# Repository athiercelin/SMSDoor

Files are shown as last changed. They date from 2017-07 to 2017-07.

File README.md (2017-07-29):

# SMS Door Control
This project allows you to build a SMS controlled door buzzer with minimal impact to existing infrastructure.

**This is an active project that will change as often as required**

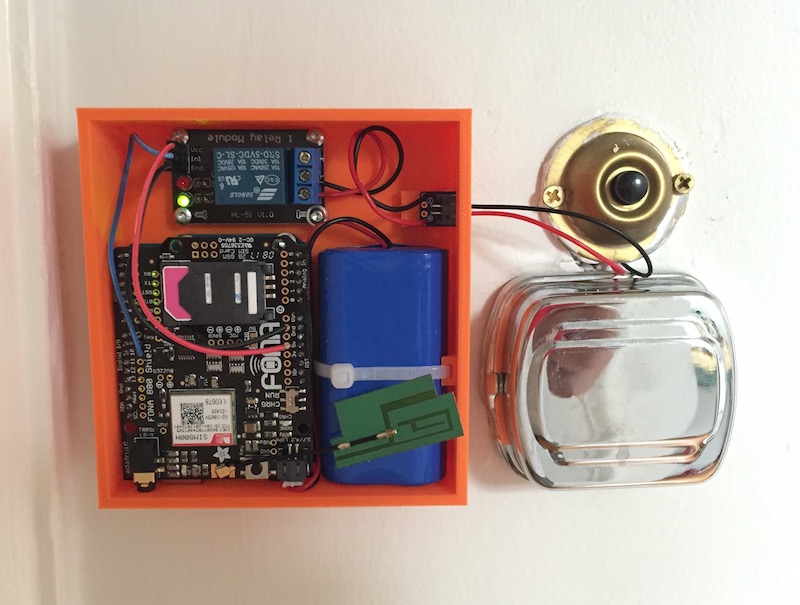
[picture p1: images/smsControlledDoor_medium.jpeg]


## Premises
I rent an old apartment in SF. There is no door man so deliveries are difficult.

To circumvent this, I created this project which allow the delivery company to gain temporary access to the lobby using a text message.

At the same time, I get notified and have remote control to the system through the text interface.

Finally, because I rent, I wanted a none intrusive and damaging system.

## Bill of Materials

|Picture|Label|Comments|
|---|----|----|
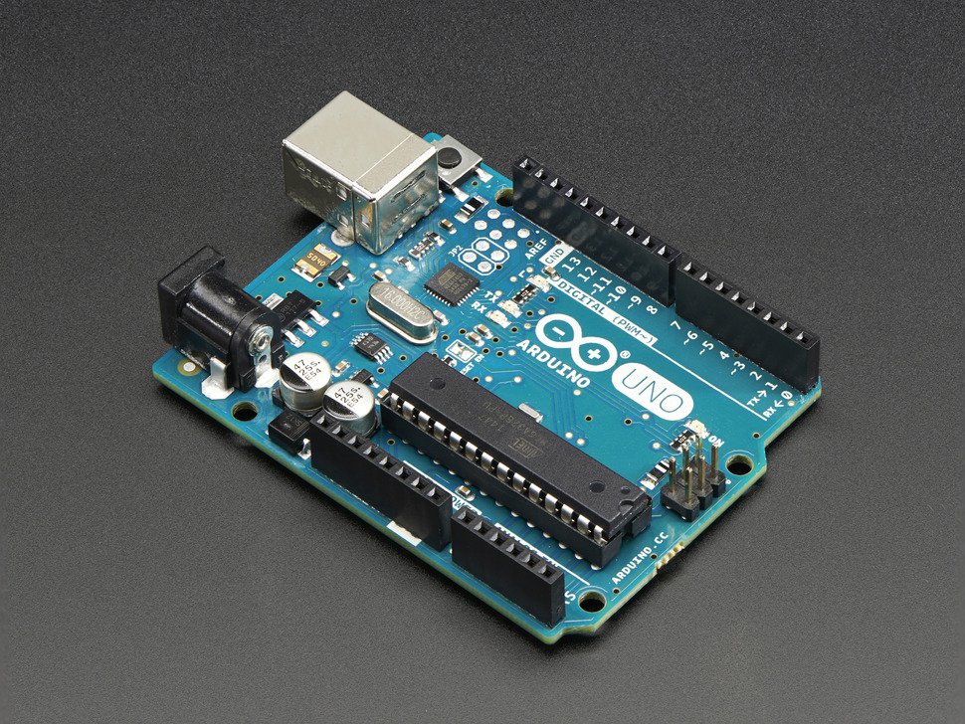
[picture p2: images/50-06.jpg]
|  | [Arduino Uno R3 (Atmega328 - assembled)](https://www.adafruit.com/product/50) | The brain of the project|
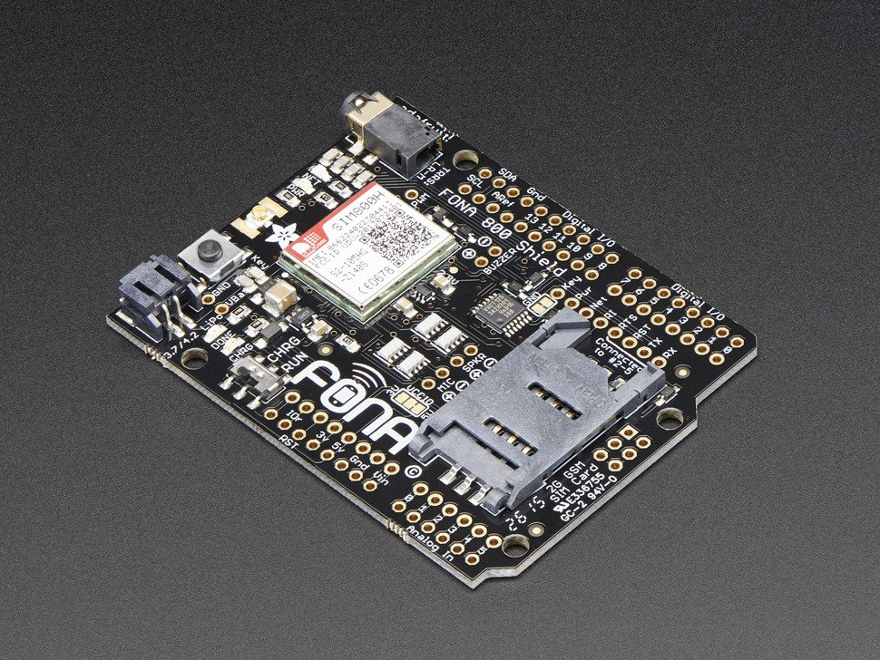
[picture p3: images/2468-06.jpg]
|  | [Adafruit FONA 800 Shield - Voice/Data Cellular GSM for Arduino](https://www.adafruit.com/product/2468) | Making your life easy to access by SMS|
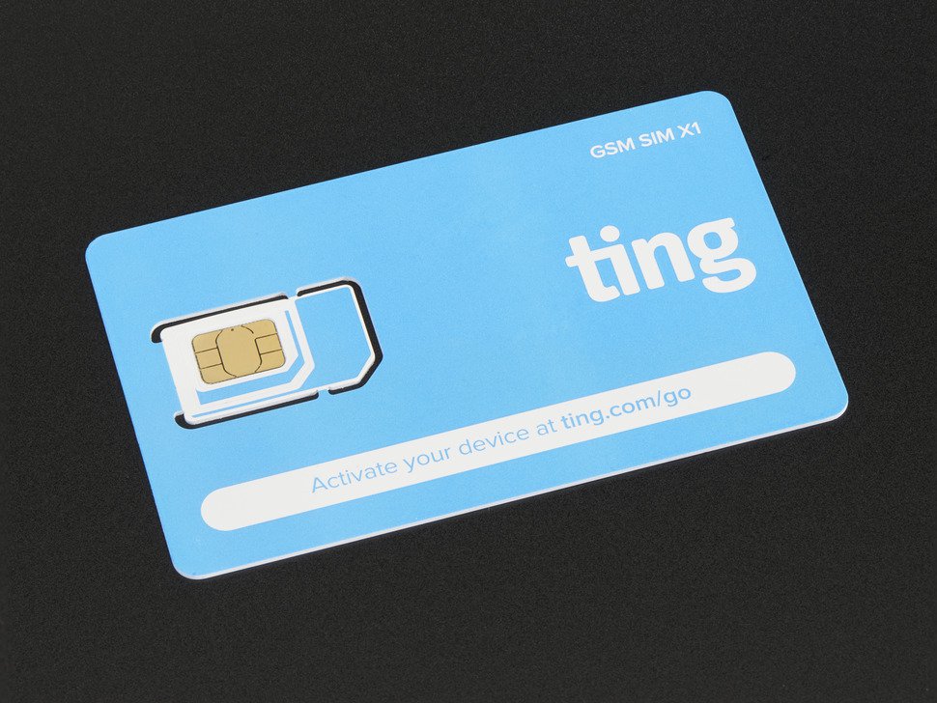
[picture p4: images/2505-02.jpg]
|  | [GSM 2G SIM Card from Ting & Adafruit - Data/Voice/Text USA Only](https://www.adafruit.com/product/2505) | Cheap plan, you can use others too |
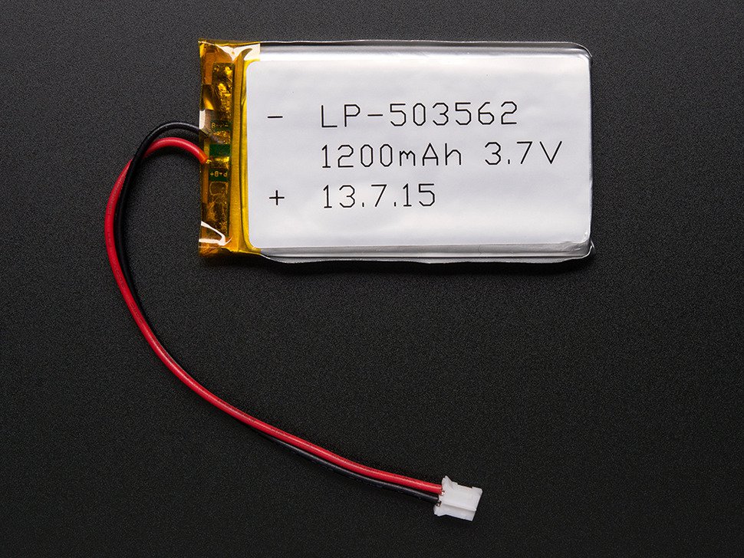
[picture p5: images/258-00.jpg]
|  | [Lithium Ion Polymer Battery - 3.7v 1200mAh](https://www.adafruit.com/product/258) | Mandatory for the GSM module |
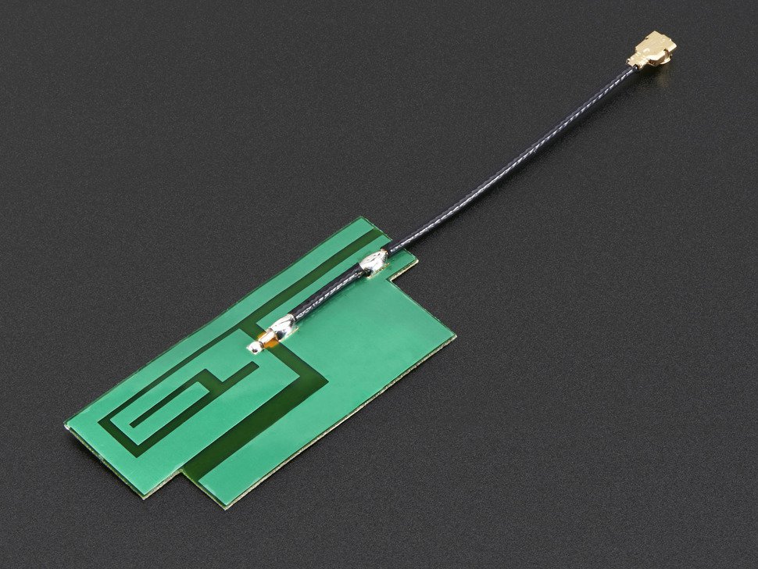
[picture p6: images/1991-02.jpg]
|  | [Slim Sticker-type GSM/Cellular Quad-Band Antenna - 3dBi uFL](https://www.adafruit.com/product/1991) | |
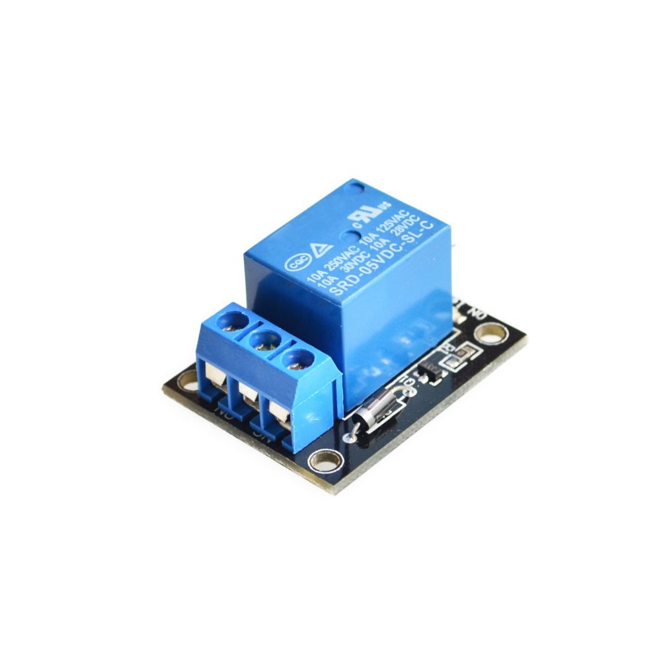
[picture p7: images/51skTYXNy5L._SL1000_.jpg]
|  | [Relay module](https://www.amazon.com/Tolako-Arduino-Indicator-Channel-Official/dp/B00VRUAHLE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) | This works with pretty much every voltages |
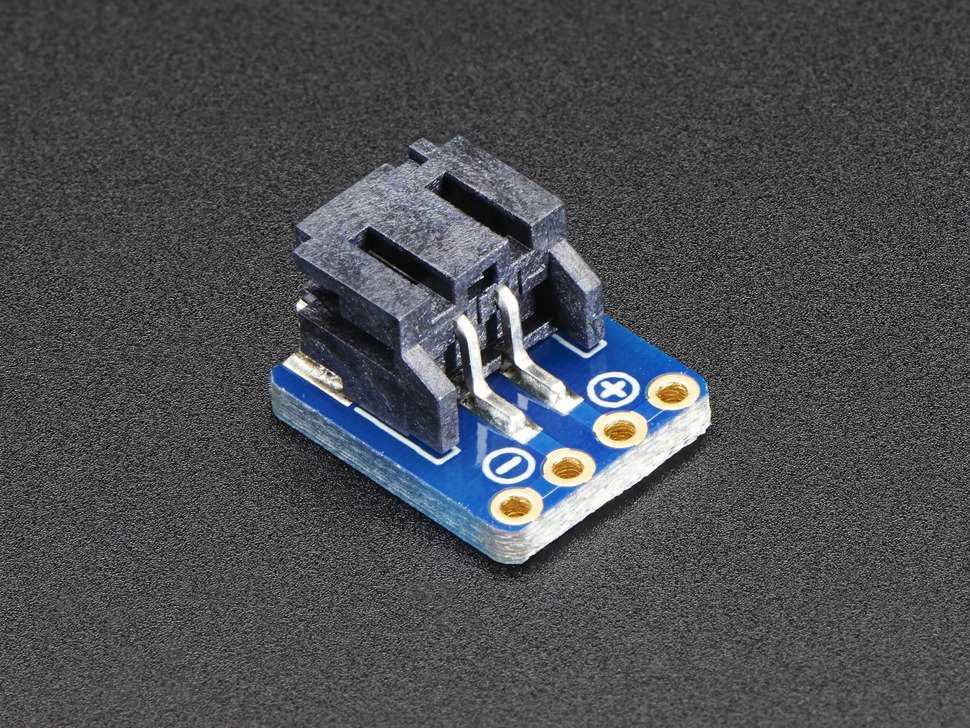
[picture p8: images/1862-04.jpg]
|  | [JST-PH 2-Pin SMT Right Angle Breakout Board](https://www.adafruit.com/product/1862) | |
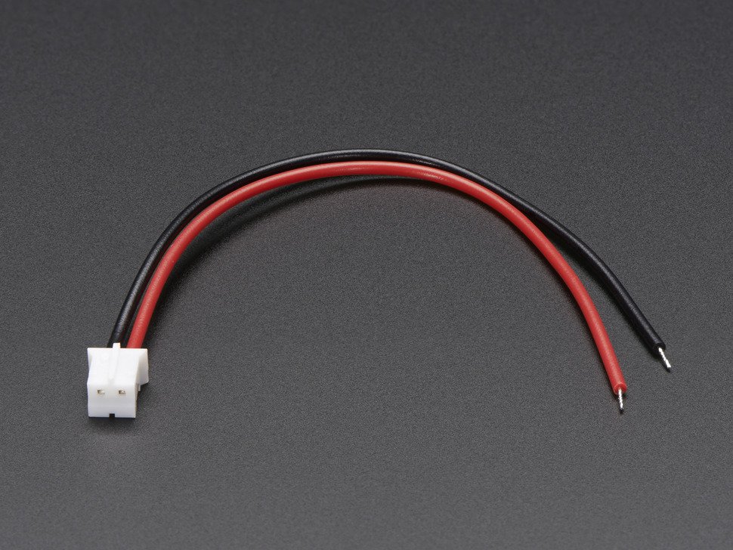
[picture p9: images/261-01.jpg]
|  | [JST 2-pin cable](https://www.adafruit.com/product/261) | I used this cable to easily dismount the Control from the door bell button. The cable get screwed to the door buzzer button inside the apartment |

## Tools Needed
You can obviously use other tools, but these are the one I used to make this project a reality.

Soldering Iron - https://www.amazon.com/AMERICAN-HAKKO-PRODUCTS-INC-FX-951/dp/B0012B8NW8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

Solder - https://www.amazon.com/Kester-24-6337-0027-Solder-Alloy-Diameter/dp/B0149K4JTY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

3D Printer - http://shop.prusa3d.com/en/3d-printers/59-original-prusa-i3-mk2-kit.html

Hot Glue Gun - https://www.amazon.com/Surebonder-PRO2-100-100-Watt-Temperature-Industrial/dp/B006IY359K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

Screws - I salvaged screws from old electronics

## Assembly
1. Print the case & lid
2. Tap the mounting hole for the boards
3. Place the battery and zip tie it
4. Screw in the relay module
5. Hot glue the JST connector into its location
6. Place the Arduino and screw it in place
7. install the sim card on the Fona and the Fona on the Arduino
7. Connect a JST cable to your door bell button
8. Place the case close and connect the JST connector.

Note: I use picture frame mounting "velcro" straps to mount the case and to be able to dismount it easily for charging and changes to the code.

## Software

I started this project using one of the sample provided by Adafruit.

What followed is a modified version to deliver the feature I wanted.

All you need to do is change the host phone number, guest code, upload the .ino into the arduino and you are good to go.

## Usage
There is two sets of access type: Guest and Host. Host is the owner of the device while guest is anyone trying to access the door with the access code.

### Guest
Guest only need to send a text with the access code you set at the begining of the file or modified using the host commands.

### Host
Host command are bound to the register phone number. It's not exactly über safe, but decent enough for the purpose.

Here are the list of the commands to be sent by text message.

`OVERRIDE`: Opens the door the exact same way the access code door for the guests.

`FLUSHSMS` : deletes all SMS.

## Questions
You can reach me on social media or in the issues here.
Checkout tinkerlocker.com.

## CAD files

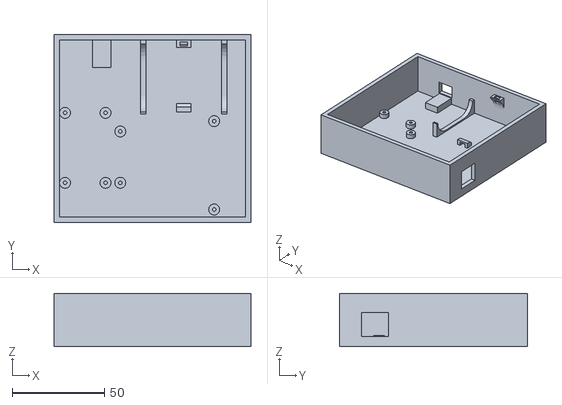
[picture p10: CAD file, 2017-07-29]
smsDoorCase.stl
107.0 x 102.0 x 29.0

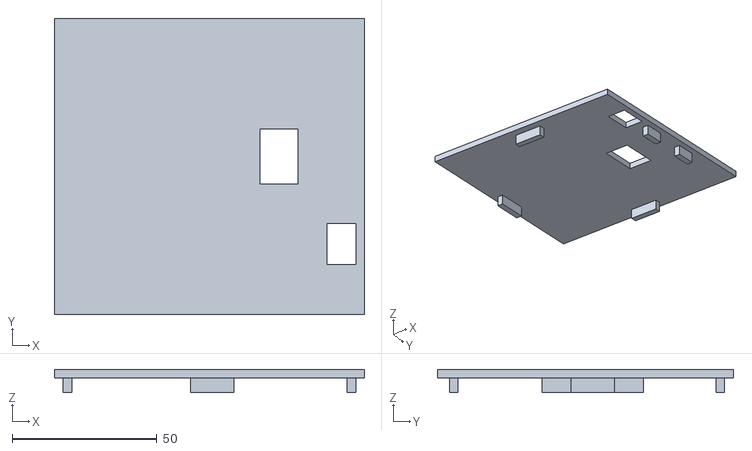
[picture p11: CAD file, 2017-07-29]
smsDoorCaseLid.stl
107.0 x 102.0 x 8.00

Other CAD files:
smsDoorCase.skp

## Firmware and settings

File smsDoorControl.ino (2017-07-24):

/*
    Written by Arnaud Thiercelin on Jul 23, 2017
    Derived from the sample code from Adafruit - see header below
    MIT license see License.md for more information
*/

/***************************************************
  This is an example for our Adafruit FONA Cellular Module

  Designed specifically to work with the Adafruit FONA
  ----> http://www.adafruit.com/products/1946
  ----> http://www.adafruit.com/products/1963
  ----> http://www.adafruit.com/products/2468
  ----> http://www.adafruit.com/products/2542

  These cellular modules use TTL Serial to communicate, 2 pins are
  required to interface
  Adafruit invests time and resources providing this open source code,
  please support Adafruit and open-source hardware by purchasing
  products from Adafruit!

  Written by Limor Fried/Ladyada for Adafruit Industries.
  BSD license, all text above must be included in any redistribution
****************************************************/

#include "Adafruit_FONA.h"

/** Settings **/
// This host ID is to be set in order to identify the owner of this SMSDoor
#define hostCallerID "+1INSERTNUMBER"

// This code is what should be sent by your host to gain access.
// It should be long enough to be secure, short enough to be type easily.
#define entryCode "123456"

// when debug mode is active, the execution is driven by the serial interface with the arduino.
#define debugMode false

// when test mode is active, the host commands are ignored so you can send guest command from the host number
#define testMode false

/** Implementation **/
#define FONA_RX 2
#define FONA_TX 3
#define FONA_RST 4

// this is a large buffer for replies
char replybuffer[255];

// We default to using software serial. If you want to use hardware serial
// (because softserial isnt supported) comment out the following three lines
// and uncomment the HardwareSerial line
#include <SoftwareSerial.h>
SoftwareSerial fonaSS = SoftwareSerial(FONA_TX, FONA_RX);
SoftwareSerial *fonaSerial = &fonaSS;

// Hardware serial is also possible!
//  HardwareSerial *fonaSerial = &Serial1;

Adafruit_FONA fona = Adafruit_FONA(FONA_RST);

uint8_t readline(char *buff, uint8_t maxbuff, uint16_t timeout = 0);

// Relay control
int relayPin = 10;

void setup() {
  if (debugMode) {
    while (!Serial);
  }

  Serial.begin(115200);
  Serial.println(F("FONA SMS caller ID test"));
  Serial.println(F("Initializing....(May take 3 seconds)"));

  // make it slow so its easy to read!
  fonaSerial->begin(4800);
  if (! fona.begin(*fonaSerial)) {
    Serial.println(F("Couldn't find FONA"));
    while (1);
  }
  Serial.println(F("FONA is OK"));

  // Print SIM card IMEI number.
  char imei[16] = {0}; // MUST use a 16 character buffer for IMEI!
  uint8_t imeiLen = fona.getIMEI(imei);
  if (imeiLen > 0) {
    Serial.print("SIM card IMEI: "); Serial.println(imei);
  }

  Serial.println("FONA Ready");

  pinMode(relayPin, OUTPUT);
  digitalWrite(relayPin, HIGH);
}

char fonaInBuffer[64];          //for notifications from the FONA

void loop() {

  char* bufPtr = fonaInBuffer;    //handy buffer pointer

  if (fona.available())      //any data available from the FONA?
  {
    int slot = 0;            //this will be the slot number of the SMS
    int charCount = 0;
    //Read the notification into fonaInBuffer
    do  {
      *bufPtr = fona.read();
      Serial.write(*bufPtr);
      delay(1);
    } while ((*bufPtr++ != '\n') && (fona.available()) && (++charCount < (sizeof(fonaInBuffer) - 1)));

    //Add a terminal NULL to the notification string
    *bufPtr = 0;

    //Scan the notification string for an SMS received notification.
    //  If it's an SMS message, we'll get the slot number in 'slot'
    if (1 == sscanf(fonaInBuffer, "+CMTI: \"SM\",%d", &slot)) {
      Serial.print("slot: "); Serial.println(slot);

      char callerIDbuffer[32];  //we'll store the SMS sender number in here

      memset(&callerIDbuffer, 0, 31);

      // Retrieve SMS sender address/phone number.
      if (! fona.getSMSSender(slot, callerIDbuffer, 31)) {
        Serial.println("Didn't find SMS message in slot!");
      }
      Serial.print(F("FROM: ")); Serial.println(callerIDbuffer);

      // Retrieve SMS value.
      uint16_t smslen;
      char messageBuffer[255];
      if (! fona.readSMS(slot, messageBuffer, 250, &smslen)) { // pass in buffer and max len!
        Serial.println("Failed reading SMS content!");
      } else {
        char *smsMessage = messageBuffer;

        smsMessage[smslen] = 0;
        // Check is callerID is Host
        if (strcmp(callerIDbuffer, hostCallerID) == 0 && testMode == false) {
          handleHostRequest(smsMessage);
        } else {
          handleGuestRequest(callerIDbuffer, smsMessage);
        }

        // delete the original msg after it is processed
        //   otherwise, we will fill up all the slots
        //   and then we won't be able to receive SMS anymore
        if (fona.deleteSMS(slot)) {
          Serial.println(F("SMS Deleted!"));
        } else {
          Serial.println(F("Couldn't delete SMS"));
        }
      }
    } else {
      Serial.print(F("Failed to get slot:"));
      Serial.println(slot);
    }
  }
}

void openDoor() {
  // Turn on pin
  digitalWrite(relayPin, LOW);

  // Wait 10s
  delay(10000);

  // Turn off pin
  digitalWrite(relayPin, HIGH);
}

/** Guest functions **/
void handleGuestRequest(char *callerID, char *smsCode) {
  // Check the message content for a valid key
  bool hasValidKey = false;

  Serial.print("SMS Received:");
  Serial.println(smsCode);

  Serial.print("FROM:");
  Serial.println(callerID);

  
  if (strcmp(smsCode, entryCode) == 0) {
    hasValidKey = true;
  } else {
    Serial.print("Failed code ");
    Serial.print(smsCode);
    Serial.print(" -> expected:");
    Serial.println(entryCode);
  }

  //Send back an automatic response based on key
  if (hasValidKey == true) {
    Serial.println("Sending Success Response...");
    if (!fona.sendSMS(callerID, "Access Granted!")) {
      Serial.println(F("Failed sending response"));
    } else {
      Serial.println(F("Sent!"));
    }
  } else {
    Serial.println("Sending Error Response...");
    if (!fona.sendSMS(callerID, "Access Denied.")) {
      Serial.println(F("Failed sending response"));
    } else {
      Serial.println(F("Sent!"));
    }
  }

  // Act on door based on key.
  if (hasValidKey == true) {
    openDoor();
    h_notifyAccess(true, callerID);
  } else {
    h_notifyAccess(false, callerID);
  }
}

/** Host Functions **/
void handleHostRequest(char *smsMessage) {
  char *cmd = strsep(&smsMessage, " ");
  char *value = smsMessage;

  Serial.print("Handling Host Command: ");
  Serial.print(cmd);
  Serial.print(", arg: ");
  Serial.println(value);

  if (!strcmp(cmd, "OVERRIDE")) { // Manual Access
    h_manualAccess();
  } else if (!strcmp(cmd, "FLUSHSMS")) {
    h_deleteAllSMS();
  } else {
    Serial.println("Unknownd Host Command");
    fona.sendSMS(hostCallerID, "Unknownd Host Command");
  }
}

// This functions notifies the host of entries.
void h_notifyAccess(bool access, char *guest) {
  if (access == true) {
    char *notifMessage = strcat("Access granted to: ", guest);

    Serial.println("Sending Success Response...");
    if (!fona.sendSMS(hostCallerID, notifMessage)) {
      Serial.println(F("Failed"));
    } else {
      Serial.println(F("Sent!"));
    }
  } else {
    char *notifMessage = strcat("Access denied to: ", guest);

    Serial.println("Sending Error Response...");
    if (!fona.sendSMS(hostCallerID, notifMessage)) {
      Serial.println(F("Failed"));
    } else {
      Serial.println(F("Sent!"));
    }
  }
}

void h_manualAccess() {
  char *notifMessage = "Manual Access Granted Sir.";
  Serial.println(notifMessage);
  if (!fona.sendSMS(hostCallerID, notifMessage)) {
    Serial.println(F("Failed"));
  } else {
    Serial.println(F("Sent!"));
  }
  openDoor();
}

void h_deleteAllSMS() {
  int slot = 0;

  for (; slot < 244; slot++) {
    if (fona.deleteSMS(slot)) {
      Serial.print(F("SMS Deleted at Slot:"));
      Serial.println(slot);
    }
  }
}

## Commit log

2017-07-09 Added Readme
    Added ino
    Started skp
    [smsDoorCase.skp]
2017-07-14 Updated cad for the case
    [smsDoorCase.skp]
2017-07-17 updated cad of case.
    [smsDoorCase.skp]
2017-07-23 Fixed minor bug with relay
    Added a header for my changes to the Adafruit sample.
    [smsDoorCase.skp]
2017-07-24 Fixed bugs
    Removed update code functionality
    [smsDoorControl.ino]
2017-07-24 Tweaks for case v3
    [smsDoorCase.skp]
2017-07-28 Updated case to mk3 designs - First fully functionning one.
    [smsDoorCase.skp]
2017-07-29 Final touches and validation on the lid
    [smsDoorCase.skp]
2017-07-29 Added final STLs
    [smsDoorCase.stl, smsDoorCaseLid.stl]
2018-03-09 latest sms door case
    [smsDoorCase.skp]
